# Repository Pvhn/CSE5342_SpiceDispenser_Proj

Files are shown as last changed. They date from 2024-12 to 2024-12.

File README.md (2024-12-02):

# This repo contains the contents of the Spice Mixer Project developed for CSE 5342/4342.

The construction of the repository is as follows:

- Documentation:
	- Contains documents that support the implementation of the source code and hardware
- Source Code
	- Contains all source code for the Spice Mixer
- Hardware:
	- Contains all 3D CAD Files as well as CAM files for the PCB

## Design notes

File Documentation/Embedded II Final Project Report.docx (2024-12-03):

Final Project Report - Automated Spice Mixer

Embedded Systems II

Fall 2024

Group 5 - Ethan Sprinkle, Peter Nguyen, Evan Guinn

# 1. Abstract

The purpose of this project was to design, code, and build an embedded project using a TM4C (TIVA C) microcontroller and external peripherals. For our project, we produced an automated spice mixer capable of dispensing spice recipes containing up to 8 different spices. This is useful for cooking applications allowing a user to quickly dispense and measure multiple spices for a given recipe. Future capabilities of the project were kept in mind during the design process so the project could be added to and improved upon in future iterations.

The concepts and techniques obtained from this project can also be expanded to apply to a wider range of dispenser applications such as pill dispensers.

# 2. System Design & Architecture

The spice mixer consists of the following major components: eight 3D printed spice containers with individual augers, a stepper-motor driven turnstile base, and a servo-actuated motor controlled dispensing mechanism. The mixer utilizes two stepper motors, a servo actuator, and two hall effect sensors to properly rotate and dispense the various spices based on a command from a user. The basic features of the system include the ability for a user to select and dispense a single spice, add/delete recipes, and save recipes. A user can perform any of these commands using a UART interface (such as Putty) to both send and receive information from the microcontroller. Spice recipes are saved using the EEPROM, allowing recipes and spice information to be retrieved upon power loss to the unit.

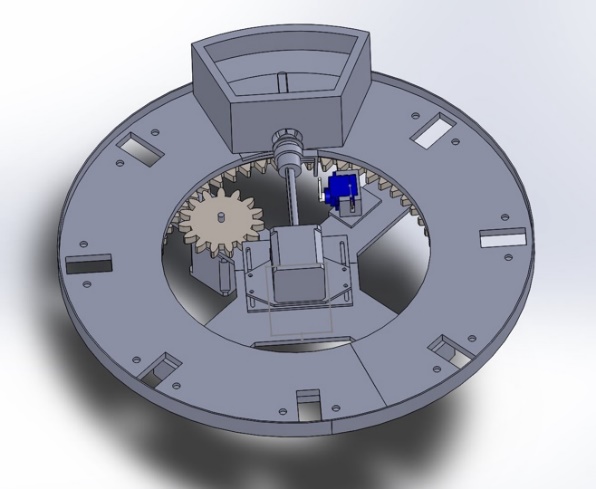
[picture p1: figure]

Figure 1. Spice Mixer CAD Design

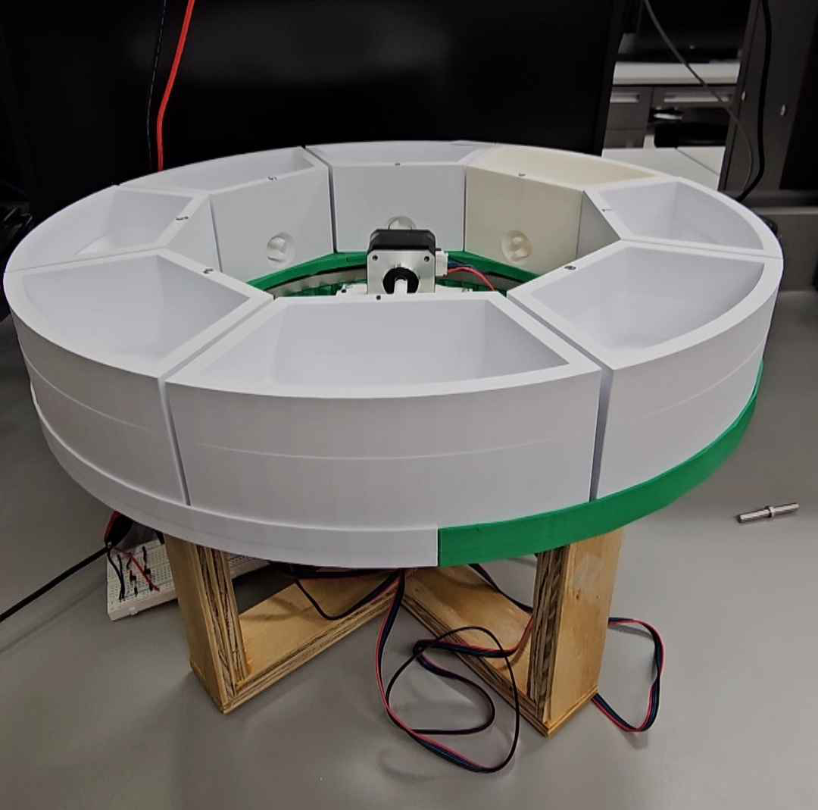
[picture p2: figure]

Figure 2. Spice Mixer

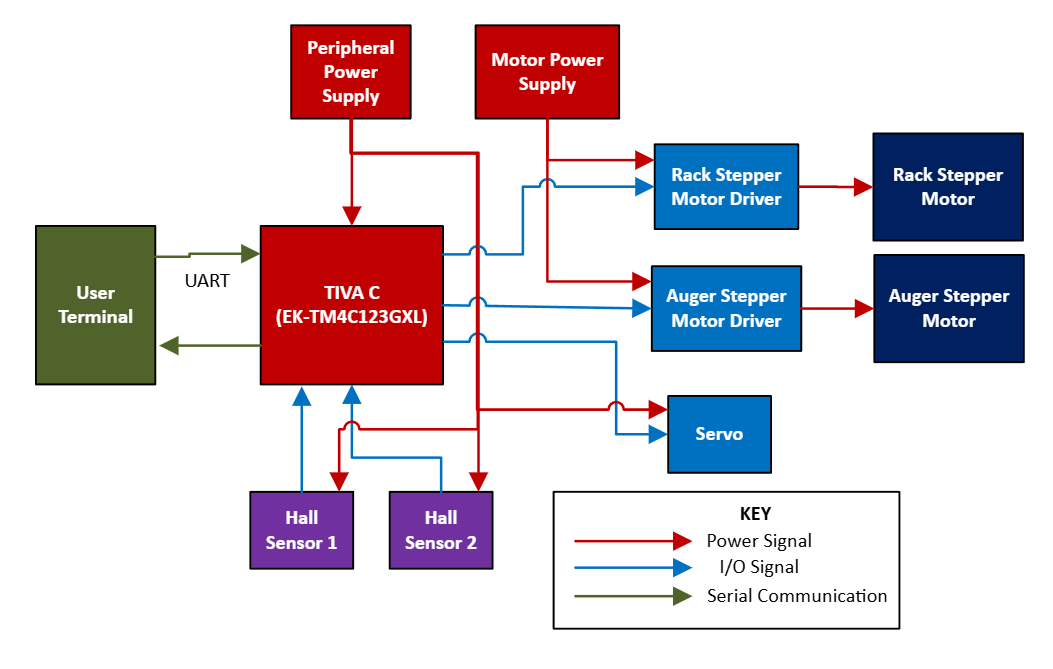
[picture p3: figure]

Figure 3. System Block Diagram

# 3. Implementation

## Hardware

### 3.1.1 Physical Components

#### Auger and Auger Shaft

Physical components of the spice mixer were modeled using SolidWorks. Shown below are the designs of the Auger and Auger Shaft mechanism which is used for dispensing spices. The auger is designed to attach to the inside of the spice holder via a small magnet placed on the end of it. The triangular points are designed to allow connection with the auger motor shaft. The opening is designed to hold approximately a volume of half teaspoon.

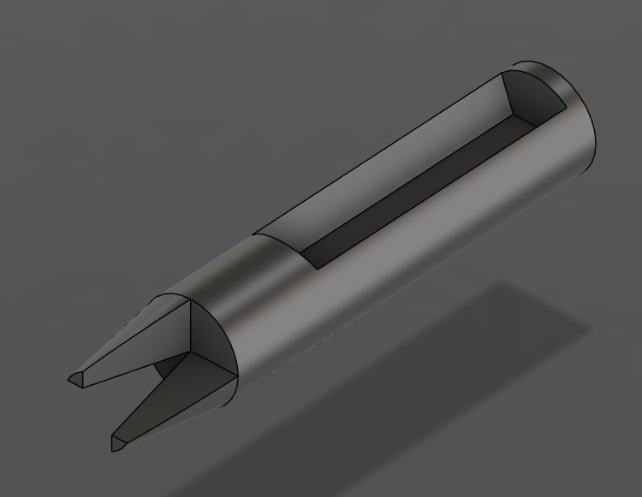
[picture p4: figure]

Figure 4. 3D Model of Auger

The auger shaft that is connected to the auger motor is designed to slide along the motor shaft using the servo. The servo controls a pinion gear which will slide the rack that the shaft is attached to.

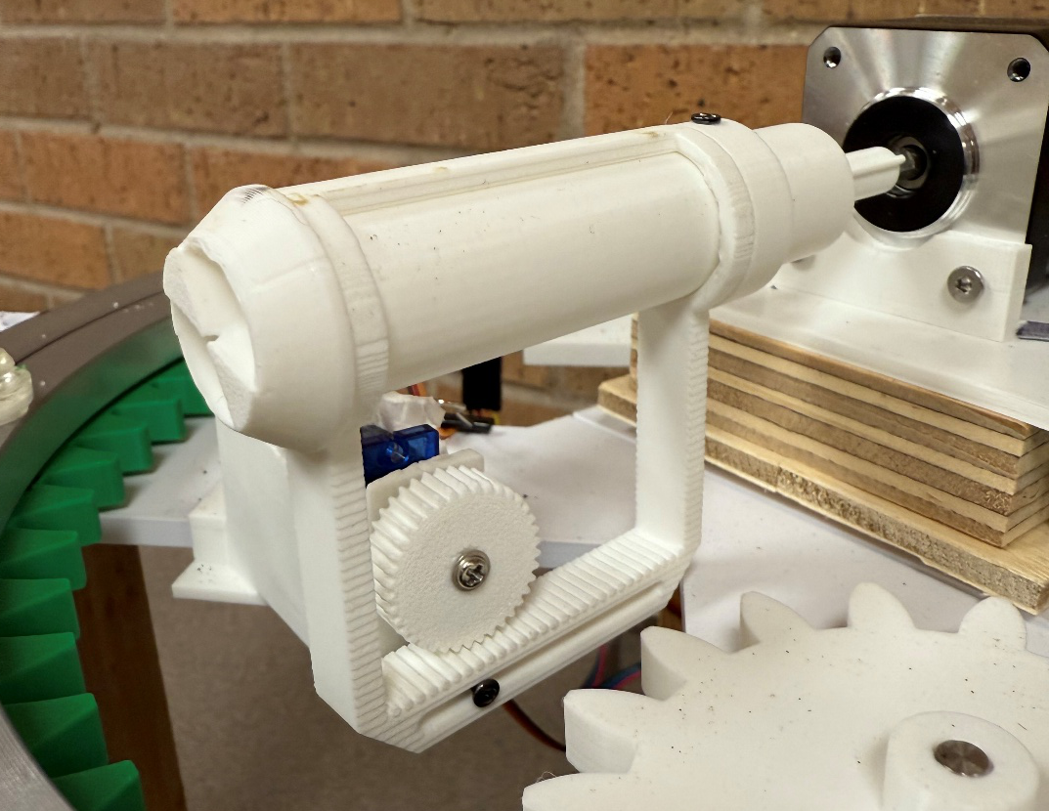
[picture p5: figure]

Figure 5. Auger Shaft and Servo Connection

#### Rack

The entire spice table sits on a turntable which is turned via gears attached to the turntable and the rack motor.

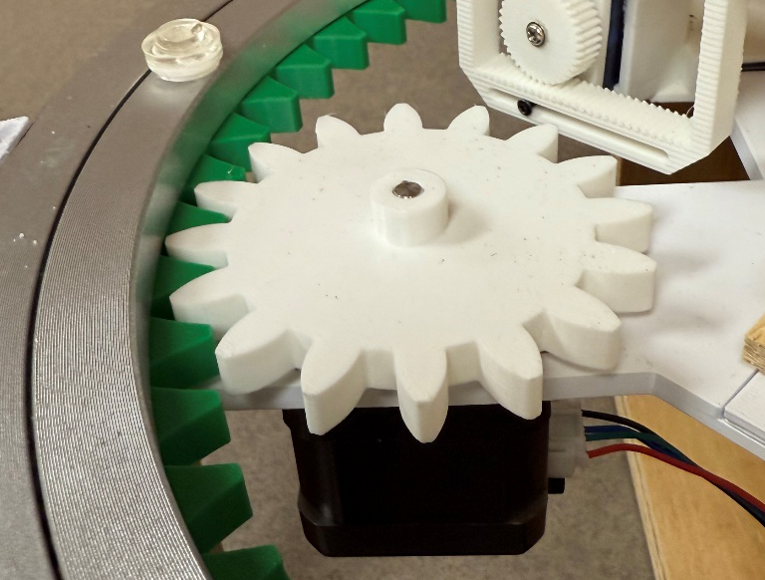
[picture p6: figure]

Figure 6. Rack Motor Gear Mechanism

### 3.1.2 Electrical Components and Peripherals

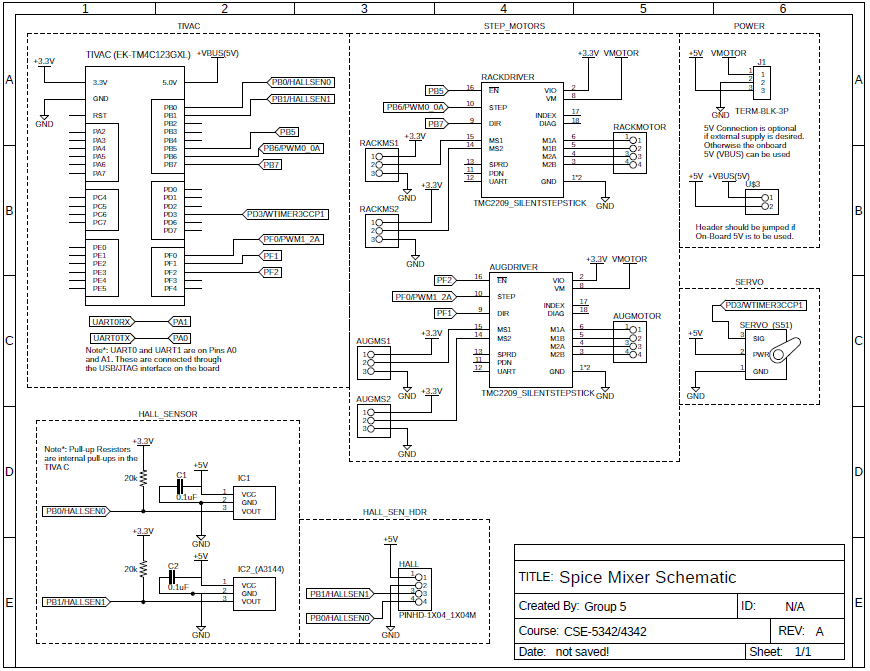
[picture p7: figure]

Figure 7. System Electrical Schematic

The figure shown above shows the overall electrical schematic of the system. The motors chosen for controlling the spice mixer are the 42BYGH NEMA 17 stepper motors. These operate at a nominal voltage of 12V and can be driven up to 1.2A max allowing for the spice mixer to be supplied with power using widely available 12 DC power supplies (commonly used by laptops and other household devices). The motors have a resolution of 1.8 degrees per step or 200 steps per revolution. The stepper motor drivers chosen for the spice mixer are the TMC2209 Silent Step-stick drivers. These are known for their silent operation and include a variety of features including a UART interface for configuring the driver. The drivers also come with on-board current sensing which is important for controlling a stepper motor and avoiding damage to the motors. Additionally, the drivers also allow for the micro-stepping of stepper motors allowing for an increased resolution per step from the base resolution. The TMC2209 allows up to a 256 microstep resolution. For the spice mixer, the configured resolution is 16 microsteps. The extended features of the driver via the UART interface were not used for the current implementation. Each driver requires a minimum of 3 pins for control, these being the step (PWM) pin, the enable pin, and the direction pin. As such at least 2 PWM pins and 4 output pins on the TIVA C are required for driving. Any of the capable PWM pins on the TIVA C can be used for driving. The pins chosen for the spice mixer were originally chosen given that each of the pins had PWM capability. During initial integration it was found that the original chosen drivers (which required 4 PWM pins each) were not suitable for the project application and thus these were replaced with the TMC2209. In consideration of time constraints and to avoid a full re-design, the original pins were re-programmed to work with the TMC2209.

The hall sensors are the A3144 Hall-Effect Sensors. Unlike linear hall sensors which have an analog output, these sensors have a digital output which operate based on an open-drain configuration, where the output pin is pulled to ground upon detection of a magnetic field and open when no magnetic field is detected. The output pins of the hall sensor are connected to input pins on the TIVA C. These input pins are configured to use the internal 20kΩ pull-up resistor to pull the sensor output high while there is no magnetic field detected. The servo used is a generic S51 servo which can be operated off a 5V supply and allows for up to 180 degrees of movement. The servo requires a 50Hz PWM signal with a duty cycle varying from 5 to 10% (pulse of 1ms to 2ms) for varying the angle. Due to the slow PWM rate required for the servo, the PWM pins of the TIVA C are not capable of driving at 50Hz without requiring a clock divisor. However, as this would impact the configuration of the stepper motor drivers, it was decided to use the wide-timers (32-bit) and its PWM output capability for controlling the servo. Communication between the TIVA C and the user is performed via UART. Module UART0 was chosen as this is directly connected to the micro-USB/JTAG output of the TIVA C board. The UART is configured to operate at the standard baud-rate of 115200 bits/s. The user may communicate using any serial terminal such as Putty or Real-Term.

### 3.1.3 Driver Board

A PCB (shown in figure 5) was made to minimize the wiring required for the spice mixer. The PCB has header pins on the bottom of the board allowing it to interface with the TIVA C as a “hat.” The driver board includes a screw terminal for the 12V motor supply and optional 5V terminal for the hall sensors and servo. If an external 5V supply is used, the jumper pin connecting the 5V rail to the TIVA C VBUS rail must be removed. In addition to this the driver board also contains jumper pins for the TMC2209 driver configuration. The pins can be moved to either apply 3.3V or GND to the MS1 and MS2 pins of the TMC2209. These pins determine the microstep resolution the driver will operate at. As stated in the previous section, the 16 microstep resolution (MS1=MS2=3.3V) is used. Refer to the datasheet of the TMC2209 driver for further configuration. The step motor drivers interface to the driver-board via header pins allowing them to easily be removed in the event it needs to be replaced. The PCB shown in figure 4 was produced in-house at UTA by the EE Makerspace Lab. As it was a prototype board, the board does not contain a silk screen or any labeling to indicate the pin connections and polarity. Connections to this board should be verified against the schematic (figure 4).

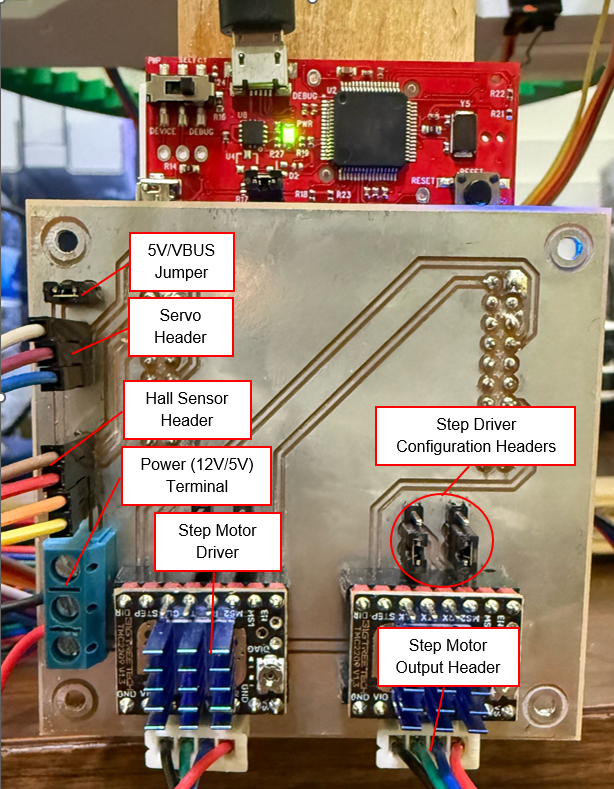
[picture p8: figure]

Figure 8. Driver Board PCB

## Software

The software is broken up into 3 primary modules consisting of the User-Interface module, the Motor Control module, and the EEPROM module. Each of the primary modules are designed specifically for the control and program flow of the Spice Mixer. The primary modules may each contain smaller secondary modules which are designed for the purpose of performing a specific action such as moving a stepper motor, reading/writing to the EEPROM, and parsing for user commands. These secondary modules can be readapted for other purposes.

### 3.1.4 UART

User commands are sent over the UART protocol from an input device, such as a computer (in the case of the prototype) or touchscreen. For the prototype, the baud rate used is 115,200, with 8N1 and a 16-entry FIFO. These commands are sent as plain text, which is then parsed into a sequence of ‘fields’ delineated by spaces and stored in a USER_DATA structure. During parsing, the positions and number of fields are stored alongside the original plain text for use by the command functions in UIControl.

### 3.1.5 User-Interface and Main Program

The user-interface/UART is designed to continuously poll for user commands in the main loop of the program. When a command is received from the UART, the user-input is parsed (as described in the UART section) and the first argument is compared and validated against a list of known commands. Any command that is not recognized by the UART interface will result in a notification error to the end user and the display of the “help page” which will list all known commands and their usage/syntax. In addition to being a known command, some commands require additional initial arguments (fields). These required minimum fields will also be validated at the time of processing the user command. An error message will also be displayed for the following conditions:

- Incorrect parameters used when entering a UART command
- The amount of spice remaining in a container is less than the amount required by a recipe
- A Recipe Name does not exist in EEPROM
- A Spice Name does not exist in EEPROM

Figure 9 shows the basic flow of the main loop. The valid system commands are discussed in the sections below.

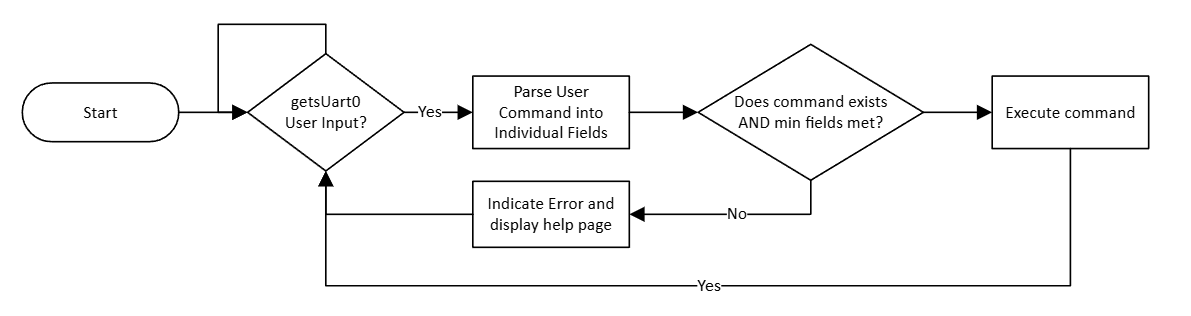
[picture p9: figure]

Figure 9. Main Loop Flow Diagram

#### Spice Command

The spice command is the basic command to dispense a single selected spice. The syntax of the spice command is as follows:

- spice <spice name> <quantity>

The user must provide the name of an existing spice followed by the quantity. If the name provided does not match any of the known spices, an error will be indicated, and the command will abort. The quantity will be checked to verify there is enough spice remaining for the requested quantity. This is done by reading the remaining quantity from the EEPROM and then comparing it. If there is an insufficient amount, an error message will be indicated to the user and the system will then request additional user action to determine if the user would like to proceed with the dispense or cancel the action. The user may respond by pressing any key to continue with the dispense or typing in “cancel” to abort the command. On completion of the dispense sequence (discussed in the Motor Control section), the remaining quantity will be updated in the EEPROM.

Note that, on start-up, this command will not be accessible to the user until the home command is performed. (See Home command below). This is to ensure the system has accurately determined the home status before attempting to dispense. Any attempts to use this command before homing is performed will result in a warning message to be indicated to the user. The command will not be performed.

#### Recipe Command

The recipe command is an advanced command to dispense multiple spices. The syntax of the recipe command is as follows:

- recipe <recipe name>

The user must provide the name of an existing recipe. No other arguments are required. If the name provided does not match any of the known spices, an error will be indicated, and the command will abort. If the name exists, the contents of the recipe will be extracted from the EEPROM. Prior to dispensing, each spice element of the recipe will be verified to ensure there is enough remaining. Like the spice command, if there is not enough, an error message will be indicated to the user and the system will prompt the user to either continue or cancel the command. This is repeated for every element in the recipe. The end of a recipe is determined either when the requested quantity is 0 (indicating an empty slot) or the max slots (8) have been dispensed. On completion of the dispense sequence, the remaining quantity of each spice is updated in the EEPROM.

Note, on start-up, this command will not be accessible to the user until the home command is performed. (See Home command below). This is to ensure the system has accurately determined the home status before attempting to dispense. Any attempts to use this command before homing is performed will result in a warning message to be indicated to the user. The command will not be performed.

#### View Command

The view command allows for the user to view a list of existing spices and their quantities or a list of stored recipes. The user can access either by indicating “spices” or “recipes” as the second argument. The syntax of the view command is as follows:

- view <items>

#### Check Command

The check command allows for the user to check the contents of an existing recipe. The user must provide the name of an existing recipe. The command will extract the contents of the recipe from the EEPROM and display each element and their quantities (in teaspoons). The syntax of the check command is as follows:

- check <name>

#### Save Command

The save command allows for the user to save a new recipe or update an existing recipe. If the name of the recipe already exists, the system will notify the user that the recipe already exists and whether they would like to continue or not. If the user chooses to cancel (by typing in cancel) then the command will abort. If the user chooses to continue, the command will begin prompting the user for entries in the recipe. If the name does not exist, the command will validate that the name entered is less than 16 characters. If it is not, the command will be aborted. If the name is within the required length, the system will begin prompting the user for entries in the recipe. The syntax of the initial command is as follows:

- save <recipe name>

For each entry, the user must provide the name of an existing spice along with a quantity less than 1 cup (48 teaspoons). The system will validate that the user enters a valid name and quantity. If either is invalid, an error message will be indicated to the user. Unlike other errors, at this stage, the error message will not abort the command. Instead, it will loop and prompt the user to try again and enter a valid entry. This will continue until either a valid entry is provided or the user cancels. The syntax of entries is as follows:

- <spice name> <quantity>

At any time, the user may type “done” instead of an entry to indicate that this is the end of the recipe. Alternatively, the user can type “cancel” to abort the command. If the user enters a spice name that they had previously already entered, the user will be notified and prompted if they would like to overwrite their previous entry. If the user chooses to continue, then their newest entry will be stored. The system will continue to prompt the user until either “done” is entered or the max number of elements (8 spices) is entered. On completion, the recipe is stored into the EEPROM. If the recipe is an update of an existing recipe, the number of stored recipes (in the EEPROM) will not be incremented. Otherwise, it is incremented. Additionally, the name of the new recipe is copied to the local list/dictionary of stored recipes.

#### Delete Recipe Command

The delete recipe command allows for a user to delete a stored recipe from the EEPROM. The syntax of the delete recipe command is as follows:

- delete <recipe name>

The user must provide the name of an existing recipe. If the name does not exist, an error will be indicated to the user and the command will be aborted. If the name does exist, the system will then ask the user to confirm that they want to delete the recipe. The user must type the keyword “delete” to continue with the removal. If any other word is entered, the system will abort the command. On entering the keyword, the system will remove the recipe from the EEPROM. Due to the direct indexing and accessing of the recipes, along with deleting the recipe, the system must subsequently copy each existing recipe below the deleted recipe and move them up one index if the recipe is in the middle of the block of existing recipes. This method is not ideal as it requires multiple read and writes of the EEPROM thus decreasing the overall usage life of the EEPROM. However, this was the most “efficient method” and as such was used. Future work may improve upon this method.

#### Refill Command

The refill command allows for the user to refill an existing spice with a specified quantity. The syntax of the refill command is as follows:

- refill <spice name> <quantity>

The user must provide the name of an existing spice followed by the quantity. If the name provided does not match any of the known spices, an error will be indicated, and the command will abort. The quantity will be checked to verify if it is less than the max allowed quantity. If the quantity is greater than the max allowed quantity, then a message will be indicated to the user indicating that the quantity they have entered is greater than the max and the system is assuming that they meant to fill the spice to the max quantity. After validation, the command will then subsequently update the remaining quantity of the spice in the EEPROM with the requested quantity.

#### Change Spice Command

The change spice command allows for the user to change or update the name of an existing spice. This is mainly used if the user has filled a spice slot with a different spice from the one currently stored in the system. The syntax of the command is as follows:

- change

On entering the command, the user is prompted for the slot value they would like to update. This slot must be between 0 and 7 (max of 8 slots). If an invalid slot number is provided, an error message will be indicated to the user and the system will prompt the user to try again and enter a valid slot number. This will repeat until either a valid slot number is entered, or the user chooses to cancel. On a valid slot number, the system will repeat the name of the spice that is currently stored in the slot number the user had entered and ask the user to confirm that they would like to continue with changing the name. If the user chooses to continue, the command will then prompt the user to enter the name of the new spice. This name must be less than 16 characters and must be one continuous word. If the entered name is invalid, an error message will be indicated to the user and the system will prompt the user again to enter a valid name. On a valid name entry, the system will write the new name to the corresponding slot in the EEPROM as well as update the local list/dictionary of known spices. The system will then ask if they would also like to update the quantity of the slot they had chosen. The user must type “done” if they wish not to continue. Otherwise, the system will begin prompting the user to enter the quantity of the spice. The user may enter cancel if they change their mind, and the command will then abort. Otherwise, if a valid quantity is entered the remaining quantity of the spice in the EEPROM will be updated with the new requested quantity.

#### Home Command

The home command performs the homing of the rack. The syntax of the home command is as follows:

- home

The command will simply perform a call to the home function in the motor control module to perform the homing. Details of the homing method are discussed in the Motor Control section below. On failure of homing the system will indicate an error message to the user to verify there are no obstructions and to either try again or power reset the system.

#### Reset Command

This command allows for the user to perform a system reset. The syntax of the reset command is as follows:

- reset

The reset command is to be used in the event of an EEPROM failure or some other system type failure. This command will reset all spices to the default first start-up values and will also remove all stored recipes. On entry to the command the user will be asked to confirm that they want to proceed with the system reset. The user must type in the reset keyword “RESET_SYSTEM_X342” to proceed with the reset. Any other value entered will result in the command to be aborted. On the entering of the keyword, the system will re-initialize the EEPROM with the default spice data (like the initialization that is performed when the system is powered on for the first time). As this reset is destructive, once the reset is complete, the system will prompt the user to restart the system. The program will then enter an infinite loop, thus forcing the user to power-cycle/restart the system.

#### Stop Command

The stop command allows for the user to remove power from all the primary stepper motors. The syntax of the stop command is as follows:

- stop

On entry of the command, power to both the Rack and Auger motors will be removed. Note, homing must be performed following the usage of this command before spice or recipe commands can be used as once the motors are turned off, the position of the rack will effectively be unknown.

### 3.1.6 Motor Control

This section discusses the Motor Control module of the spice mixer. The motor control module includes all functions necessary for controlling the stepper motors and the servo, as well as reading the inputs from the hall-effect sensors.

#### Dispense Sequence

When a recipe or spice is selected to be dispensed, there are 4 major aspects of the dispense sequence. These are: positioning the rack, engaging the servo, commanding the auger dispense, and the disengaging of the servo.

The microcontroller first checks its current position and compares it to the desired position of the selected spice. The program will perform a delta calculation to obtain the shortest distance and determine if it should turn clockwise or counterclockwise (whichever is closer to the desired position). Once the delta has been calculated, the required angle is converted into microsteps to be used by the PWM Interrupt handler for commanding the rack motor. Note, the chosen microstep resolution for the Spice Mixer was 16. The conversion from an angle to microsteps would normally be performed using the following equation:

(∆angle)/(200*16) (1)(Angle to Microsteps Equation)

Where 200 as recalled is the number of full-sized steps for a full rotation of the motor shaft. However, since the rack motor is connected to the rack via a gear, the conversion must also account for the gear ratio. As designed, the gear ratio is 56:15 where the rack motor must make 3.5 turns for a full rotation of the rack motor. The previous equation now becomes:

(∆angle)/(200*16)*GearRatio (2)(Angle to Microstep w/ GearRatio Equation)

Once all rotation steps have been completed (and the auger is aligned with the shaft of the motor dispenser), the servo actuates the auger motor shaft into place with the auger of the spice dispenser. The auger will then be commanded to turn the desired number of rotations. Note, a full rotation of the auger motor equates to a ½ teaspoon of the selected spice. The rotation command is like the rack motor except that the auger motor only needs to rotate one direction, so the delta calculation is simply calculating the total number of microsteps per requested rotations. Equation 1 can be used for this conversion. Once rotation is complete, the servo will then disengage the motor shaft from the auger and the process will repeat for any additional spices in a recipe. The figure below shows the overview of the dispense sequence. Note, due to the auger shaft sometimes not being properly aligned with the auger, an auger offset was added in the software. The auger motor will complete the requested number of rotations and then will rotate an additional 20 degrees to offset the auger. The servo will disengage at this point. After disengagement, the auger motor will rotate the shaft back 20 degrees. This placement positions the auger approximately in the middle of the opening of the auger shaft thus increasing the likelihood of a successful connection.

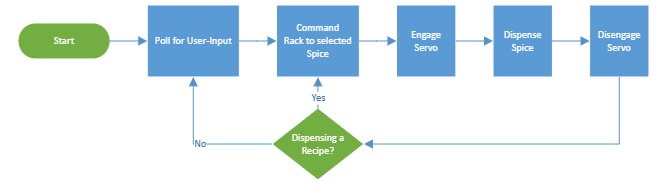
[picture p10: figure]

Figure 10. Dispensing Sequence Flowchart

#### Stepper Motor Control

The stepper motors are controlled by the TMC2209 stepper motor drivers. These require at least 3 inputs which are: STEP, EN, and DIR. The step pin is the PWM input which is used to control the speed and step sequencing of the stepper motors. Speed itself is not controlled by varying the duty cycle. Instead, speed is controlled by increasing or decreasing the PWM frequency since for each pulse detected the driver will increment the step index to move the motor. The duty cycle output from the TIVA C is fixed at a 50% duty cycle. The EN pin is the enable pin and is used to enable/disable the stepper driver output. The DIR pin is the direction pin and is used to control the direction of the motor (CW = 0, CCW = 1).

The commanding and controlling of the PWM outputs are performed via a PWM Interrupt. The beginning of a motor command starts with the calculation of microsteps required by the command. For the instance of the rack motor, it will be provided a slot position (0-7) that it needs to move to. The slot position is then converted to the angle on the rack with respect to the home position. The difference between the requested angle and the current position is taken. The delta is used to determine the direction of rotation (CW or CCW, whichever is the shortest distance). For the instance of the auger motor, it will be provided the number of rotations. The angle/number of rotations is then converted to microsteps of which are provided to the PWM Interrupt Handler for sequencing. Once calculation is complete, the EN pin is cleared to enable the stepper driver output and the PWM Interrupt is enabled to begin the driving of the motor. The main program at this point enters a while loop and will poll the status of the motor while it waits for the step command to be completed by the interrupt handler.

Figure 11 Stepper Motor Control Flowchart

The PWM Interrupts are configured to interrupt when the generator value reaches 0. This is used since the duty cycle is always fixed at 50%. On an interrupt, the handler will determine if it needs to run based on the step count (previously calculated by the main program). If the step count is greater than 0, this indicates the interrupt should continue to run and sequence the step pulse to the driver. With each interrupt, the step count is decremented until it reaches 0, at which point the interrupt handler will disable further interrupts and disable the PWM output to the stepper driver. In addition to decrementing the step count, the interrupt handler is also responsible for updating the speed of the motor (by setting the LOAD and CMPX registers of the PWM module to vary the frequency). This ensures a consistent PWM output as the interrupt handler will sync the output. The interrupt handlers are mostly the same for both the stepper motors with the exception being that the rack motor has acceleration control. The choice of using interrupts vs actively managing the motor control in the main program was made with the intention of performing other tasks such as active homing or failure handling cases, such as when the user may issue a “stop’ command.

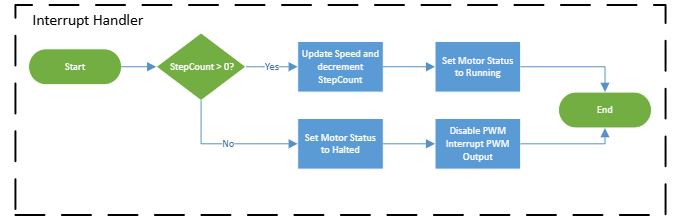
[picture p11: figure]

Figure 12. PWM Interrupt Handler Flowchart

To allow for a common architecture and provide the potential for expansion, all necessary data for motor control is stored in a structure type. A motor can be “registered” into the system by adding it to the Motor Data array. Each motor has the following available properties:

- Run Status – (OFF, HALTED, RUNNING, FAILED)
- Direction – (CW, CCW)
- Home Status – (NOTHOME, NEARHOME, HOME)
- Steps - (The number of steps the motor needs to move)
- Position – (Not used in current implementation. Was kept with the intention of using for active position feedback).
- Speed – (speed in rpm)

Not all properties are used by a motor (such as the Home Status and position for the auger motor). This motor data is only accessible by the stepper motor control module. This was done to limit access to important motor control data. “Get” functions were developed to allow external modules to read the status.

Acceleration control of the rack motor was added to improve accuracy and prevent skipping of steps during start and stop maneuvers due to the inertia of the rack. A simplified flowchart of the acceleration control algorithm is shown below.

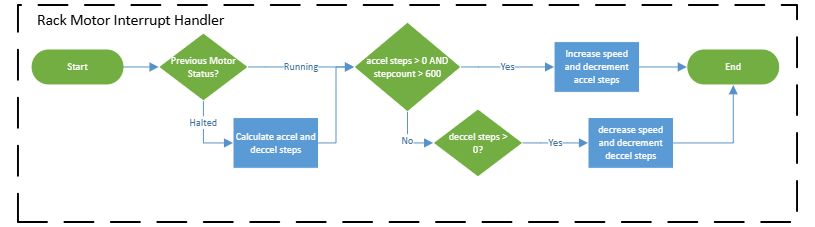
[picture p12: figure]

Figure 13. Acceleration Control Flowchart

The algorithm begins by determining the previous status of the motor. If the motor status was previously halted, then the acceleration/deceleration steps are calculated. This is simply the amount of command steps divided by 2 for both (i.e. the motor will accelerate for half of the steps and then decelerate for the remaining half). The speed will also be set to the minimum RPM (6 RPM). In the subsequent iterations, the speed of the motor will slowly be increased by a constant factor of 0.03125 RPM (corresponding to 1 RPM increase for every 1.8 degrees). The speed will continue to increase until either the motor has reached the full commanded speed, the total number of acceleration steps has been performed, or the remaining commanded steps is less than 600. The 600 remaining commanded steps condition was added to improve control for smaller moves (such as that performed during the homing offset) as the motor has less time to decelerate in these moves. Once acceleration is completed, the motor will then begin to decelerate as it approaches the midpoint between the final position. Like the acceleration component, deceleration will decrease the speed by a constant factor. This factor is determined based on the final speed of the motor during acceleration divided by the total deceleration steps. This is done to prevent the motor from reaching the minimum speed too early in the deceleration, resulting in the motor moving into position extremely slowly during longer commands.

#### Rack Homing

On startup and/or after a stop command was issued, the Spice Mixer will require the user to initialize the calibrated “home” position before any dispense action can be performed. The homing method utilizes the mid-point between two hall effect sensors to determine the “home” position for additional accuracy. Using a single sensor may incur directional error since the hall sensor may indicate detection even if the magnet is not directly over the sensor, so by using two sensors the directional error is cancelled out since the mid-point between the two sensors will always be the mid-point regardless of the direction the rack was moving. A magnet placed under the turn table is used to trigger the sensors.

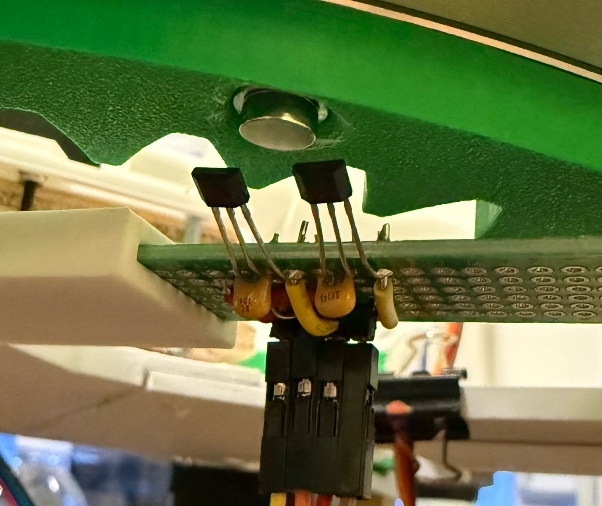
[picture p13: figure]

Figure 14. Hall Sensors and the Homing Magnet

Due to the placement of the sensors, the mid-point of the sensors is not the true home-point. Once the hall sensors have both detected the magnet, the rack motor must be commanded some additional steps to put it in the true home position.

The home state has 3 possible states: NOT_HOME, NEAR_HOME, and HOME. When one of the sensors detects the magnet, the home state will transition to NEAR_HOME indicating to the system to prepare to stop. When both sensors detect the magnet, the home state will then transition to the HOME state indicating to the system to halt the rack motor. If the home state has transitioned to NEAR_HOME and one or more sensors stop detecting the magnet, the home state will transition back to NOT_HOME, indicating to the system to speed up and continue rotation.

The checking of the hall sensors is performed via a GPIO interrupt. Since the time at which the home point is detected is critical to obtaining an accurate home position, the usage of interrupts for this is required. The interrupt is configured to trigger on both rising and falling edges. Recall from the Hardware implementation section that the Hall sensors are active low and thus their logic states are inverted. The detection of the falling edge allows us to determine when a sensor has detected the homing magnet. The rising edge allows us to determine the opposite. This is mainly used for the scenario that the hall sensor stopped detecting the magnet and reset the home status to indicate from NEAR_HOME to back to NOT_HOME. Note, this interrupt will continue to run even if a homing command is not currently being performed. This has minimal impact on the system resources as the magnet is placed in a specific position and thus it will not constantly interrupt (unless there is a failure). The usage of the interrupt may be useful in future work to perform active homing which may be used to provide positioning feedback to adjust for any error that may have incurred during normal operation.

On the issuance of a home command, the program will command the rack motor to perform 3 full rotations at a speed of 10 RPM. It will then wait approximately 1ms for the motor to begin moving to ensure an accurate motor status is obtained. The function will then continue to periodically poll the home status (that is set by interrupt) and the run status of the rack motor to determine if homing was successful or failed. If the run status of the motor indicates HALTED and the home status indicates NOT_HOME, then this indicates that the rack performed 3 full rotations before home was found. In the event of a home failure, an error code of 0xDEAF is returned to the main program for processing and failure management. If the home status indicates HOME, the function will then command the rack to rotate an additional number of steps to align with the true home position. Note, the number of steps is largely dependent on the placement of the hall sensors. For the current implementation this offset was found to be approximately 32 degrees counterclockwise.

#### Servo Control

The servo used to actuate the auger motor shaft is controlled using the Wide-Timer 3 PWM Output of the TIVA C. Unlike the Stepper motors which used an interrupt routine for controlling and maintaining the step count, the servo only requires us to set the necessary duty cycle with no further action needed. The servo operates at a rate of 50Hz and requires a pulse lasting between 1ms to 2ms (0 to 180 degrees). The conversion from desired angle to load value to be written to the TxMATCHR register of the wide timer is calculated as follows:

load value=[(desired angle)/180*((SYSCLOCK)/(50Hz)*0.1)]+((SYSCLOCK)/50)*0.025

SYSCLOCK is simply the frequency of the system (40Mhz for our case). The 0.025 factor is derived from the 2.5% duty cycle bias for a 0-degree command.

### 3.1.7 EEPROM

This section discusses the EEPROM Control module of the spice mixer. The EEPROM module is used to store system data for the spice mixer and most importantly recipes. The EEPROM is a non-volatile type of memory, i.e., it retains its data even when power is removed.

The EEPROM of the TIVA C is distributed into “blocks” where each block contains a specified number of 32-bit words. The TIVA C contains 16 total blocks with each containing eight 32-bit words. This equates to a total of 128 32-bit words. Read and write access of the EEPROM is performed in 32-bit words. The data used by the spice mixer, however, does not need to be 32-bits. To maximize memory storage, the spice mixer data is stored using smaller 16-bit words and bitfields. The memory layout of the EEPROM is shown below.

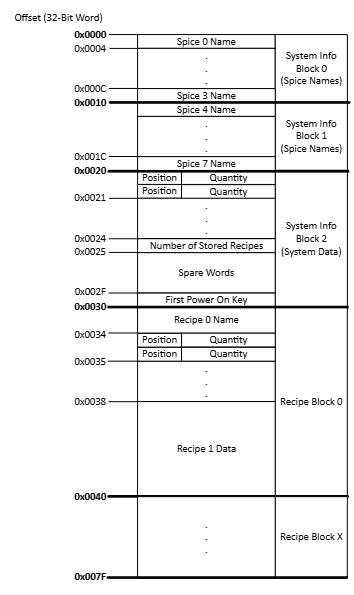
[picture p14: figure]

Figure 15. EEPROM Memory Layout

#### System Information Blocks

The system information blocks (blocks 0-2) contain data needed for operation of the spice mixer. This includes spice names, spice quantities, and the total number of stored recipes. Each of the 8 spice names are allotted four 32-bit words of memory, allowing for up to 15 characters plus the null character to be stored. The spice data is stored in a single 16-bit word. The spice data word is further split into the position and quantity bits with position being the first 4 bits of the word and the remaining 12 bits being the quantity. As the max slot capacity of the current implementation is 8, it was decided to only use 4 bits. However, this can be increased to 8-bits to support an increase in slot capacity. The quantity bits allow up to a quantity of 4096 to be stored. This is more than sufficient for the needs of the system as the max capacity is only 96 (half teaspoons). The number of stored recipes is also stored as a single 16-bit word. The full 16-bit word is not needed to store the number. However, it was decided to use the full word to simplify the reading of the number. In addition to this data, there is also a First Power-On Key that is stored in the system information block. This key is used to initialize the EEPROM with default spice data/names for the case of when it is the first time powering on the system as the EEPROM will not have anything stored in it yet. After this initial power-on, a keyword of 0xBEEF is written to the EEPROM to indicate for the next start-up that it is already initialized and should use the data currently stored in the EEPROM. The remainder of block 2 is unused. This is not only to maintain separation of system information and the stored recipes but also allows for future expansion if additional slots are added to the mixer.

#### Recipe Information Blocks

Recipe Information is stored in blocks 3 to the end of the EEPROM. As seen from the memory map, each recipe data contains the name (15 characters plus null) of the recipe, and 8 16-bit spice data words (one for each capable slot). This results in each recipe requiring a total of eight 32-bit words. Given this and the max EEPROM size of 128 32-bit words, the system has the capability to store up to 26 recipes. Not all 8 spice data words need to be used in a recipe. Unused words will be written to 0 allowing for the simple detection of the end of a recipe (when the quantity is 0). Additionally, spice data does not necessarily need to be stored in order of slots as the position bits will contain the necessary value to determine which spice to dispense.

#### Reading and Writing to EEPROM

Since the EEPROM is only accessible in 32-bit words, special considerations must be made when reading and writing to the EEPROM.

Reading from the EEPROM is simpler than a write request in that we do not need to worry about data loss. For instance, say we want to read the spice data for slot position 0. From the memory map this is stored at offset 0x0020. To initiate a read, we must write to the EEBLOCK and EEOFFSET registers. The EEBLOCK is provided the desired block number our data is in (block 2 in this instance). The EEOFFSET register is the 32-bit word offset we would like to read from (Word 0 in this instance). The read data will be returned as a 32-bit word. Per the memory map, we know that spice data for position 0 is stored in the lower half of the 32-bit word so we only need to read the data from that half. The upper half of the 32-bit word (which contains spice data for position 1) is simply ignored.

Writing data to the EEPROM requires the additional step of reading the data currently in the EEPROM. Since writing to the EEPROM is performed in 32-bits, we must ensure that the lower or upper half of the word we are not writing to is not overwritten with zeroes. By first reading the full 32-bit word and then making a local copy, we can then write data to the desired upper or lower half and then write the full 32-bit word back, thus maintaining the data. Additionally, all functions that write to the EEPROM will also return an error code from the EEPROM if the EEPROM failed to write. This error code may be used for notifying the user of a system issue and have them attempt to restart the Spice Mixer to attempt to reset the EEPROM.

# 4. Results & Testing

The physical components of the project were first modeled in Solidworks3D to ensure proper design dimensions and functionality. Parts were then 3D printed using PLA material and then tested for form, fit, and function with the rest of the assembly. Parts that failed were adjusted in the CAD software and reprinted. A wooden frame was used to elevate and hold the Spice Mixer assembly.

Software development was shared across the team using a git repository. Branches were created, tested, and merged by individual group members for the development of three main functionalities: EEPROM, UART Interface, and Motor Control. The Motor Control function was used to test and calibrate the physical components to ensure they would work properly with the software. Prior to validating the motor control with the hardware, the debugger was used to validate proper commands and outputs and ensure no hazardous faults (such as a short to ground) were being done. This was performed by verifying the state of the output registers. Additionally, appropriate timing/frequency were verified using an oscilloscope.

Once the software was validated, the motor control functions were integrated with the hardware. Electrical components and wiring were verified using a breadboard. The prototype PCB was developed afterwards once all connections were verified. The EEPROM storage was validated by first developing and testing the write functions by writing test data to the EEPROM. The read functions were then developed and tested by reading the data from the EEPROM. Proper functionality is confirmed when the value that was written to the EEPROM is repeated back by the read functions. The UART interface commands were tested individually to ensure validation of commands and ensure consistent user operation.

## Integration Findings

Integrated testing revealed some design flaws in the system. Some of these issues were corrected while others are documented here with the intention of improving it in future work.

During initial integration it was found that the stepper motor drivers initially chosen were not sufficient for the application. The drivers lacked current sensing/limiting which is critical for stepper motor control and preventing damage to both the motor and the system. This issue was corrected by choosing proper drivers (the TMC2209). Due to the difference in requirements for driving the motor control code was completely redesigned to work with the TMC2209.

Initially, the rack motor had no acceleration control. Instead, it was immediately commanded to the requested speed (like the auger motor). This was found to cause the rack motor to skip steps during start and stops resulting in inaccurate positioning during both homing and regular operation. This issue was corrected by implementing the acceleration control (described in the Motor Control section).

Variances in the 3D components led to inaccuracies in positioning. For example, it was noted that at certain positions in the rack rotation, the rack would “rub” against the outer wall. This indicated that the rack was not entirely circular. Due to time constraints, this issue was not corrected. It was also noted that the stepper motor provided enough torque to overcome this resistance and as such no further action was taken.

The original design of the auger shaft and auger required that the positioning of the shaft was perfectly aligned. This mostly resulted in the auger shaft failing to engage the auger. This issue was mitigated through both hardware and software. The hardware mitigation was to increase the area of the auger shaft. The size of the auger shaft was slightly increased thus in turn increasing the opening for the auger to connect to. The software mitigation would offset the auger screw, and then rotate the auger shaft back in the opposite direction by the same distance to position the opening of the shaft approximately in the middle of the auger screw, thus increasing the chances of a successful connection.

The flat bottom of the spice holders results in some of the contents not being fully dispensed as there is nothing to push it into the auger opening. As re-designing this would require significant redesign of the current structure, it was decided to defer this issue for future work as the purpose of this project was to develop a prototype.

# 5. Conclusions & Future Work

The main goal of this project was to design and build a functional prototype spice mixer, where additional capabilities could be added in the future to improve upon the original design. To reduce printing material costs and simplify testing, the current iteration of the mixer is limited to 8 different spices. This amount could easily be doubled to 16 containers by simply reducing the size of the current containers and updating the source code, which was designed to be easily configurable. Furthermore, the current augers were designed to dispense in ½ teaspoon amounts, but this value could be lowered by either reprinting the augers with smaller buckets, or by adding blocks to the augers to reduce their overall capacity. Additionally, with the proven functionality, focus can also be placed on improving the design of the spice holder to ensure all spices are dispensed. This may include designing so that the inside sharply slopes inward towards the auger opening thus allowing for the contents of the spice holder to naturally fall into the opening via gravity.

Currently, there is not a precise method to detect the amount of spice remaining in a container beyond a rudimentary decrement method for each auger rotation. By using this method, the system assumes that a full amount is dispensed with each auger rotation and cannot account for scenarios where the full amount is not dispensed, such as with clumping of powdered spices. Conversely, if another peripheral such as a weight scale were added, there could be a check between the expected and actual weights and the mixer could account for the calculated difference.

The UART interface provides a cheap and quick method to communicate with the spice mixer; however, it is not very user friendly. An ideal solution would be to replace the UART interface with an LCD touchscreen equipped with a GUI. This would allow easier parsing of data such as remaining spice levels, current recipes, and recipe modification. A more advanced interface could also include voice activation capability, allowing the user to speak commands to the mixer.

As previously discussed, the drivers used for the project contain advanced capabilities which can be accessed via the UART. These capabilities include stall detection and step indexing for positioning feedback. As these drivers were selected late in the project, the full capabilities of the drivers were not utilized. These features may be beneficial in providing enhanced positioning accuracy for the rack as well as for safety/failure management.

Overall, the project was designed specifically for dispensing spices. However, the concepts as well as the code baseline can easily be re-adapted for any number of dispenser type applications.

# 6. Appendices

## Source Code Repository

The following is the link to the GitHub repository containing the work described in this report. This includes all source code, documentation, and 3D CAD and CAM files.

https://github.com/Pvhn/CSE5342_SpiceDispenser_Proj.git

## Schematics and PCB Files

Development of the electrical schematic and PCB were done in Fusion 360. The following link provides copies of these files. NOTE: Fusion 360 is required for proper viewing and editing. In addition to these links, these files can also be found in the repository

Fusion 360 Project:

https://a360.co/3CVfpxP

Electrical Schematic:

https://a360.co/3AWSpOs

PCB Design:

https://a360.co/3ViIjOJ

## Demo Video

Attached is a video demonstrating the different commands. This video can also be found in the Source Code Repository (See Appendix 6.1).

Commands in the video are shown in the following order:

1. home
2. view spices
3. spice xxx
4. view recipes
5. check CAJUN
6. recipe CAJUN
7. view spices
8. save CHICKEN
  1. Saving a new recipe. For demo purposes the recipe is a random selection of spices with quantities 1,2,3, and 4.
9. view recipe
10. check recipe
11. recipe CHICKEN
12. delete CHICKEN
13. view recipes
14. change
  1. Shown in the video we are swapping out slot 2 (previously GARLIC) for our new spice “PICKLE”
15. refill SAGE 20

Link to demo video: EE5342_SpiceMix_Demo.mp4 (https://mavsuta-my.sharepoint.com/:v:/g/personal/peter_nguyen3_mavs_uta_edu/EVefTSrf9KpFvghp_Y4DllgBElhwOAp0LO3sR-mjClhxzw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)

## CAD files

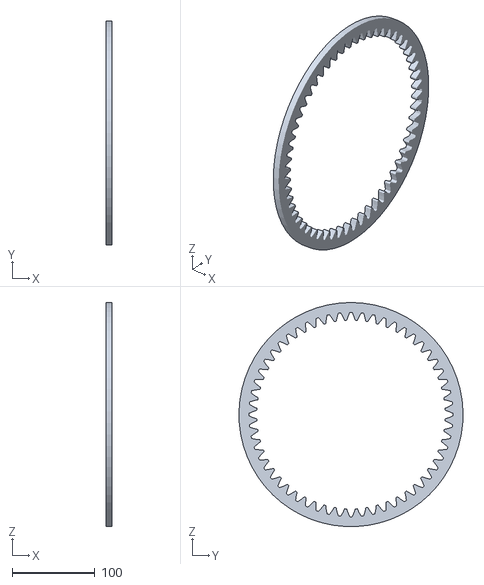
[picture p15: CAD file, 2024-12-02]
Hardware/CAD_Files/Internal gear.STL
7.62 x 271.4 x 271.3

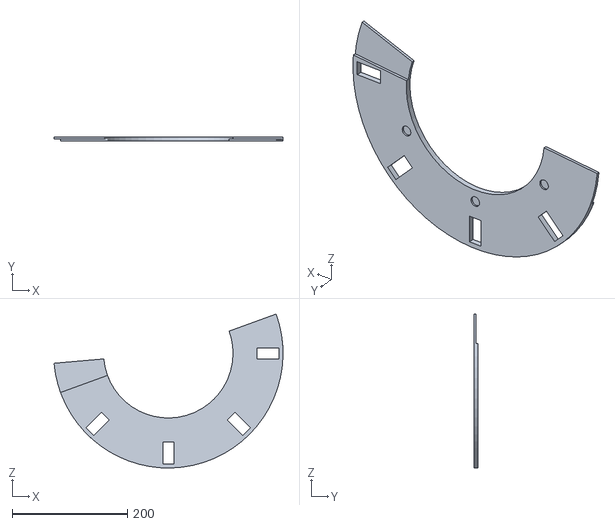
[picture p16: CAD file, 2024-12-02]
Hardware/CAD_Files/Spice Base half.STL
397.9 x 7.62 x 267.5

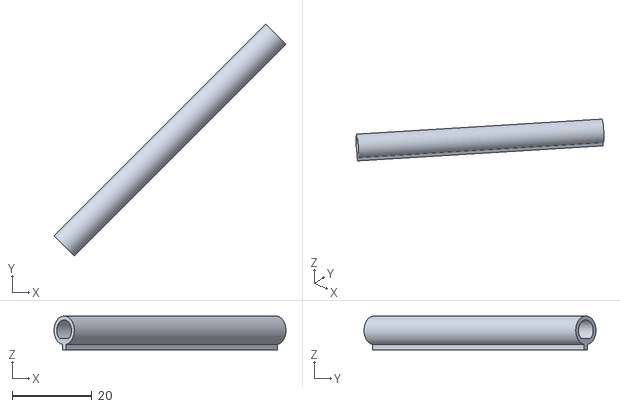
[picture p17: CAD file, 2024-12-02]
Hardware/CAD_Files/Auger Shaft.stl
58.1 x 58.1 x 8.52

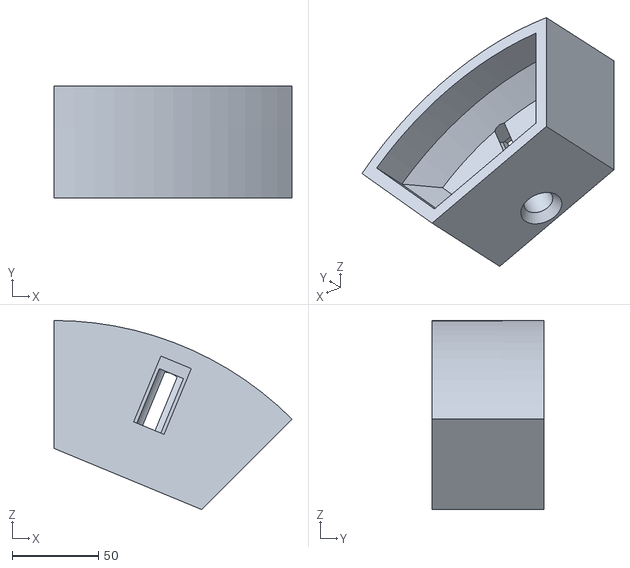
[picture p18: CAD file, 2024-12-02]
Hardware/CAD_Files/Spice Holder.STL
137.8 x 64.8 x 109.5

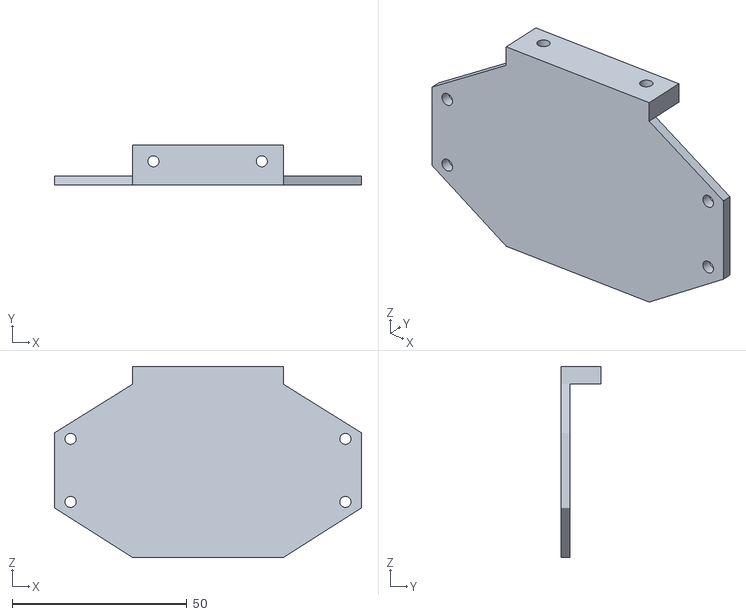
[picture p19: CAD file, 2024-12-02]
Hardware/CAD_Files/Motor1 Base1.STL
87.9 x 11.4 x 54.7

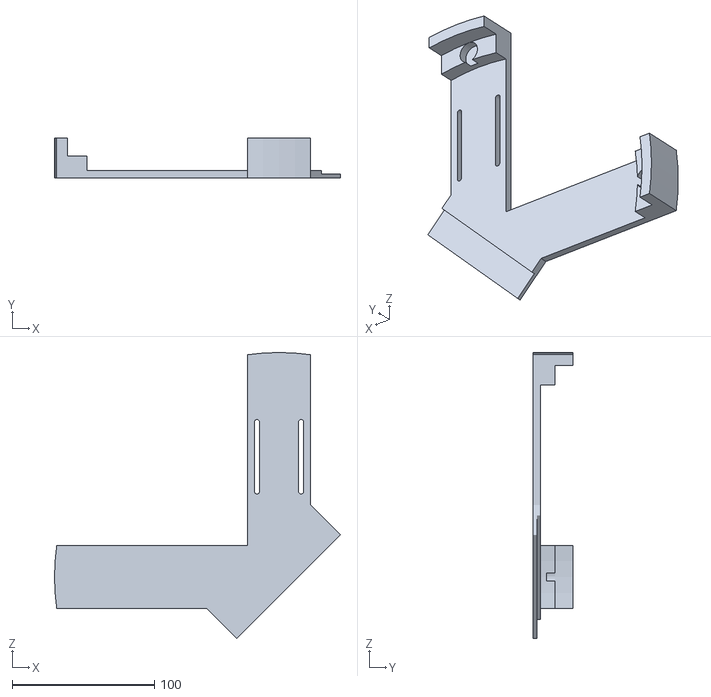
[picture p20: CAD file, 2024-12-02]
Hardware/CAD_Files/Turntable Base Half2.STL
200.7 x 27.8 x 200.7

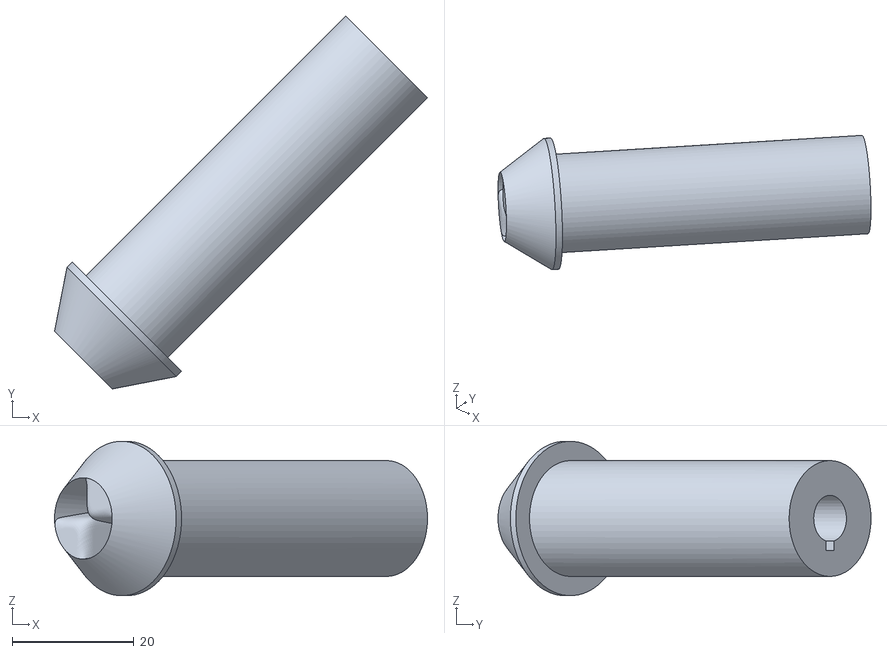
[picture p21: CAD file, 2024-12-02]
Hardware/CAD_Files/Shaft Extension.STL
61.4 x 61.4 x 25.4

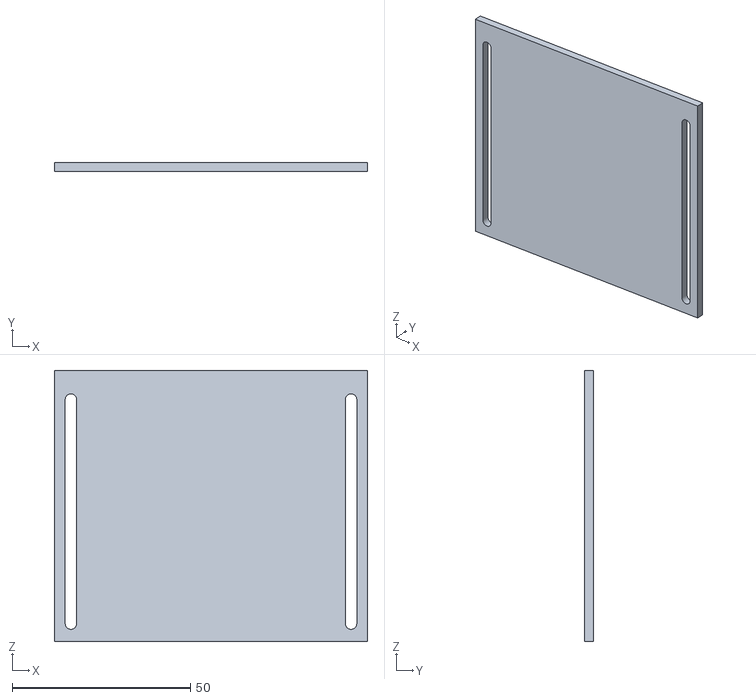
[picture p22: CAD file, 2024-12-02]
Hardware/CAD_Files/Motor1 Base2.STL
87.9 x 2.54 x 76.2

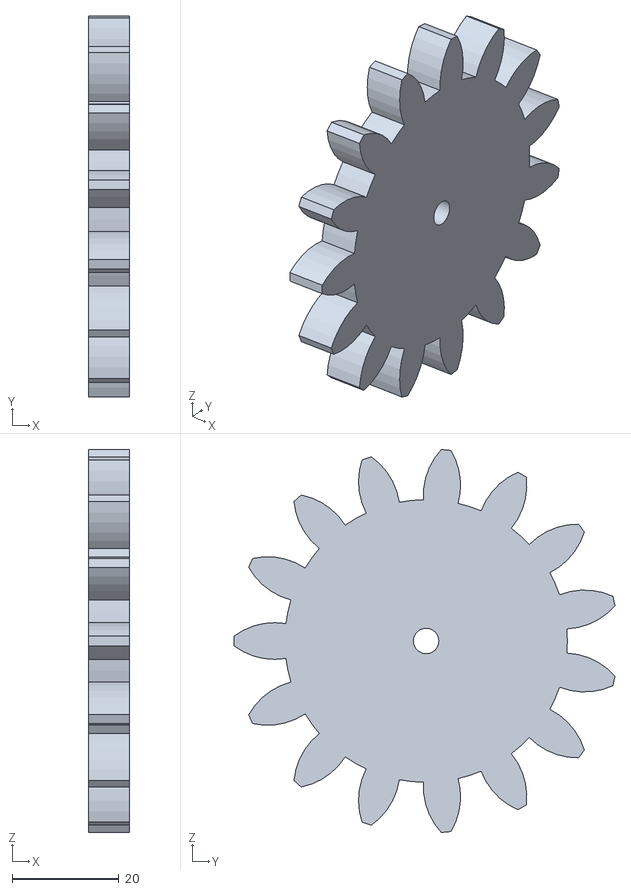
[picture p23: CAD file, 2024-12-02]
Hardware/CAD_Files/spur gear_ai.STL
7.62 x 71.3 x 71.7

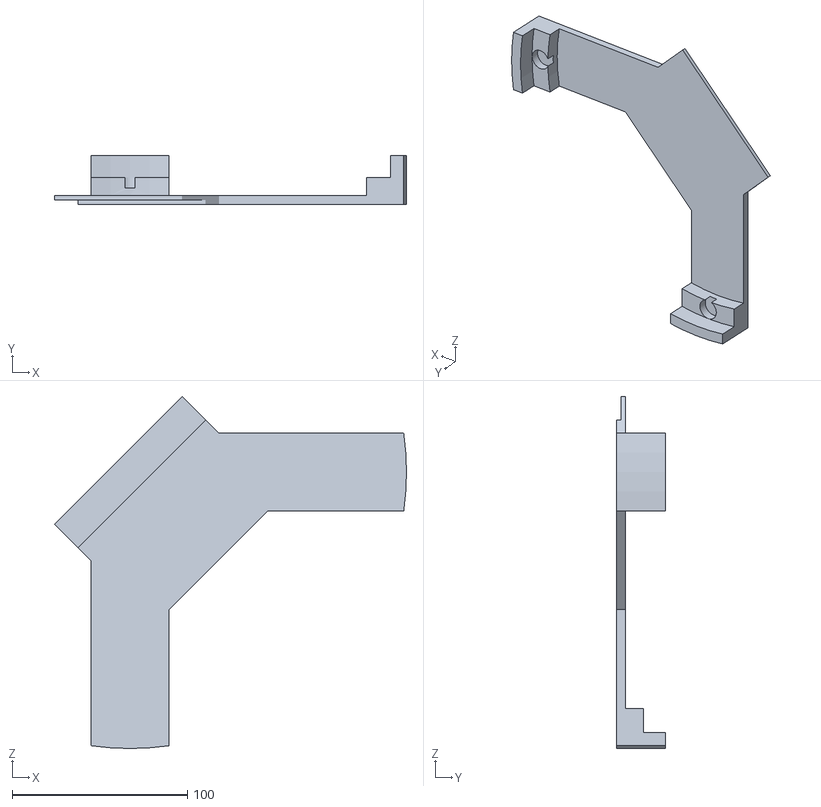
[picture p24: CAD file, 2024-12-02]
Hardware/CAD_Files/Turntable Base Half1.STL
200.7 x 27.8 x 200.7

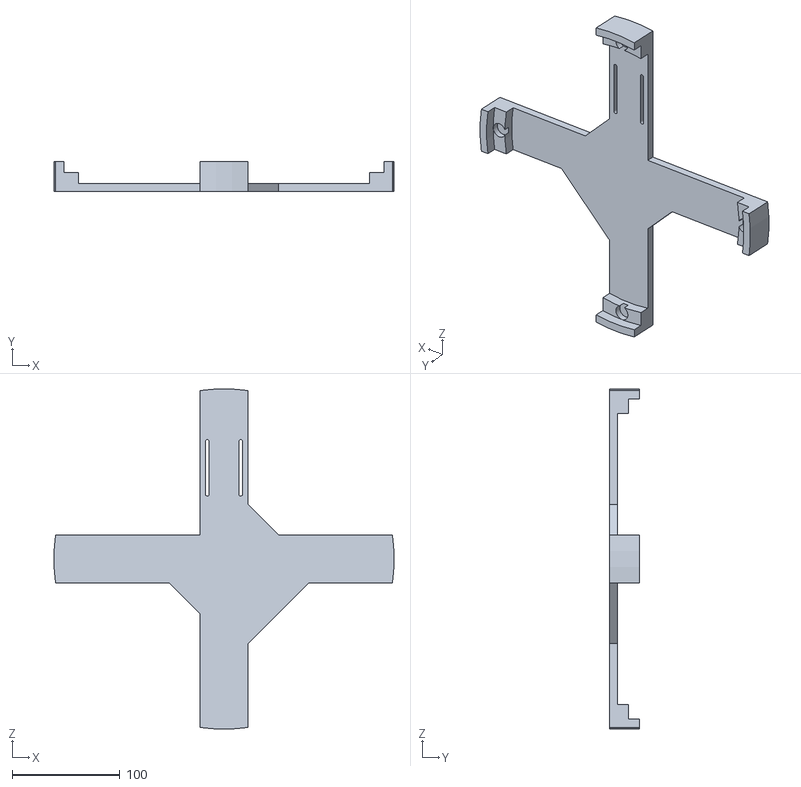
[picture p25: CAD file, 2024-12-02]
Hardware/CAD_Files/Turntable Base.STL
314.9 x 27.8 x 314.9

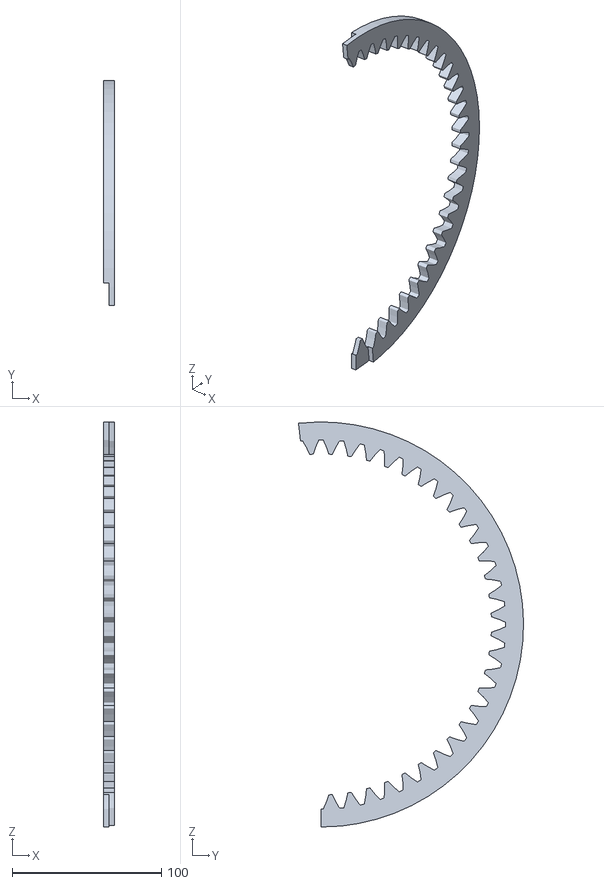
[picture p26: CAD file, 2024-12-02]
Hardware/CAD_Files/Internal gear half.STL
7.62 x 150.9 x 271.5

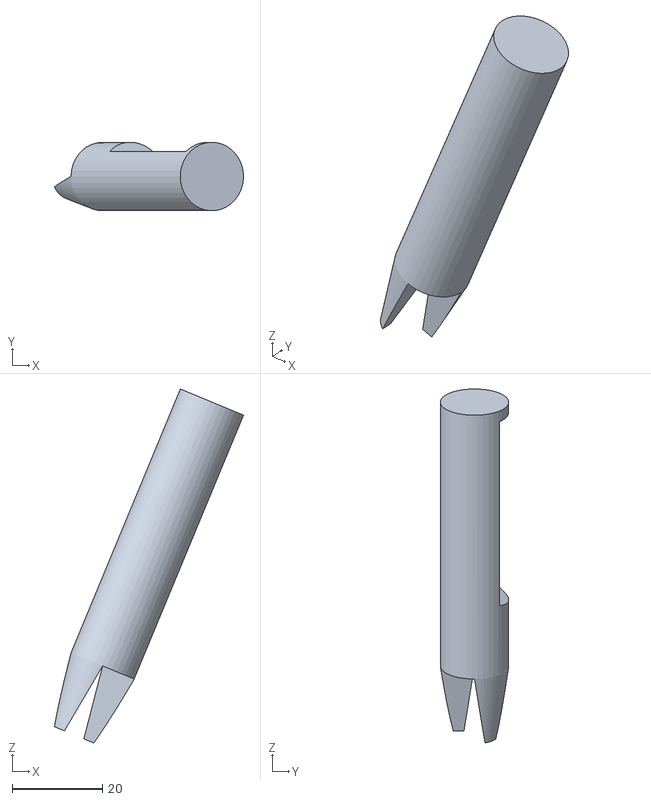
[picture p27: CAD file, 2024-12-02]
Hardware/CAD_Files/Auger.STL
41.9 x 15.2 x 78.4

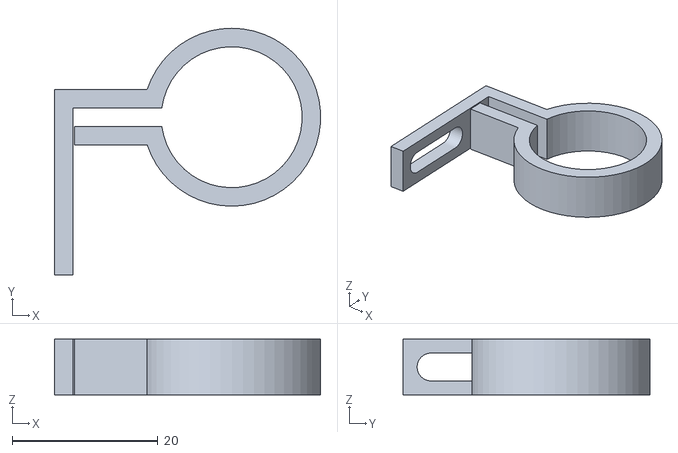
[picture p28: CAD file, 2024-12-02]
Hardware/CAD_Files/Clutch.STL
36.4 x 33.8 x 7.62

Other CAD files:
Hardware/CAD_Files/Spice Base.STL

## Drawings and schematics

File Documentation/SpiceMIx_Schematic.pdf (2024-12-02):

## PB0 PB1 PB2 PB3 PB4 PB5 PB6 PB7

INDEX | 17 DIR 9 | STEP 10 | PDN 11 | UART 12 | SPRD 13 | MS2 14 | MS1 15 | EN 16 | DIAG | 18 AUGDRIVER | GND | 1*2 VIO | 2 M1B | 5 M1A | 6 M2A | 4 M2B | 3 VM | 8

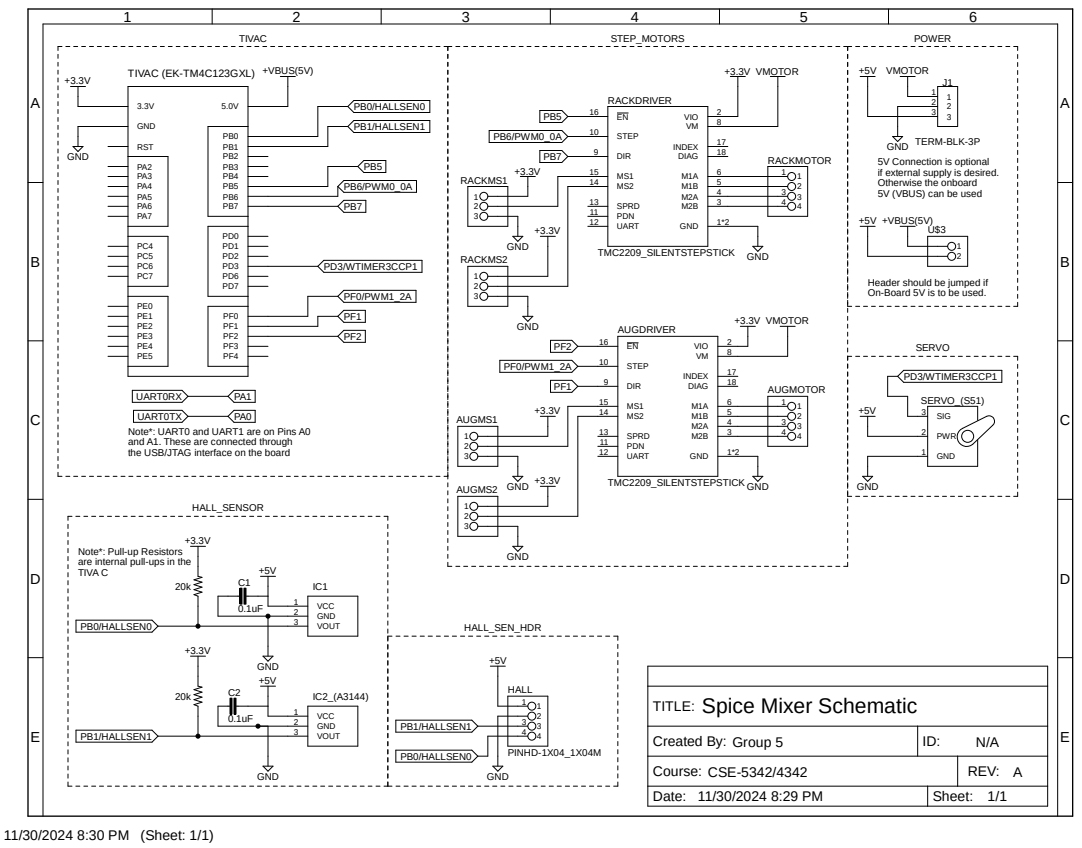
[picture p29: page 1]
11/30/2024 8:30 PM (Sheet: 1/1); STEP_MOTORS; POWER; SERVO; HALL_SEN_HDR; TIVAC; HALL_SENSOR; GND; +3.3V VMOTOR; +VBUS(5V); TMC2209_SILENTSTEPSTICK; +5V VMOTOR; PINHD-1X04_1X04M; 3.3V GND; 5.0V RST; RACKDRIVER GND; 1*2 VIO; INDEX; 17 DIR 9; STEP 10; PDN 11; UART 12; SPRD 13; DIAG; RACKMS1; 1 2 3 RACKMS2; 1 2 3 AUGMS1; 1 2 3 AUGMS2; RACKMOTOR; 2 SERVO_(S51) PWR 2; SIG 3; GND 1 HALL; IC1VCC 1; GND 2; VOUT 3; IC2_(A3144) VCC 1; PF0/PWM1_2A; PB6/PWM0_0A; PD3/WTIMER3CCP1; PB0/HALLSEN0; PB1/HALLSEN1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

TERM-BLK-3P GND
5V Connection is optional
if external supply is desired.
Otherwise the onboard
5V (VBUS) can be used
4 AUGMOTOR

Header should be jumped if
On-Board 5V is to be used.

UART0RX
UART0TX
Note*: UART0 and UART1 are on Pins A0
and A1. These are connected through
the USB/JTAG interface on the board

Note*: Pull-up Resistors
are internal pull-ups in the
TIVA C

Spice Mixer Schematic

Created By: Group 5 | ID: N/A

Course: CSE-5342/4342 | REV: A
Date: | Sheet: 11/30/2024 8:29 PM 1/1

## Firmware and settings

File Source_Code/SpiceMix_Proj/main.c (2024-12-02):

/* =======================================================
 * File Name: main.c
 * =======================================================
 * File Description: Main Program File
 * =======================================================
 */

#include <stdint.h>
#include <stdio.h>
#include <stdbool.h>
#include <string.h>
#include <stdlib.h>
#include "System.h"
#include "StepMotor.h"
#include "Servo.h"
#include "MotorControl.h"
#include "eepromControl.h"
#include "eeprom.h"
#include "uart0.h"
#include "parsing.h"
#include "UIControl.h"

#define NUMOFCMDS 11

// If a command is added here, don't forget to add
// verbage to the displayHelpPage function for syntax usage.
UICmdStructType commands[NUMOFCMDS] = 
{
    {"spice",  3},
    {"recipe", 2},
    {"view",   2},
    {"check",  2},
    {"save",   2},
    {"delete", 2},
    {"refill", 3},
    {"change", 1},
    {"home",   1},
    {"reset",  1},
    {"stop",   1},
};

void displayHelpPage(void)
{
    putsUart0("=====================================================================\n");
    putsUart0("Here are all the available commands and their usage:\n");
    putsUart0("=====================================================================\n");
    putsUart0("\n");
    putsUart0("spice <name> <qty>   - Dispenses the qty of a defined spice.\n");
    putsUart0("                       Note: qty is in half-teaspoon measurements.\n");
    putsUart0("\n");
    putsUart0("recipe <name>        - Dispenses the specified recipe.\n");
    putsUart0("\n");
    putsUart0("view <item>          - View a list of stored items. view Spices will \n");
    putsUart0("                       display a list of the stored spices and their \n");
    putsUart0("                       remaining quantities. view Recipes will display \n");
    putsUart0("                       a list of stored recipes\n");
    putsUart0("\n");
    putsUart0("check <recipe>       - View the elements of a stored recipe. <recipe> \n");
    putsUart0("                       must be the name of a stored recipe.\n");
    putsUart0("\n");
    putsUart0("save <recipe>        - Save a new recipe or update an existing recipe \n");
    putsUart0("                       <recipe> can either be a new name or the name \n");
    putsUart0("                       of an existing recipe\n");
    putsUart0("\n");
    putsUart0("delete <recipe>      - Delete an existing recipe <recipe> must be the \n");
    putsUart0("                       name of a stored recipe.\n");
    putsUart0("\n");
    putsUart0("refill <spice> <qty> - Refill a spice with a specified quantity \n");
    putsUart0("                       <spice> must be the name of an existing spice \n");
    putsUart0("\n");
    putsUart0("change               - Change or Update the name of an existing spice \n");
    putsUart0("\n");
    putsUart0("home                 - Perform the homing of the rack to reset the \n");
    putsUart0("                       the home position \n");
    putsUart0("\n");
    putsUart0("reset                - Reset the system. This will reset the system \n");
    putsUart0("                       back to the default values. This will also \n");
    putsUart0("                       remove all stored recipes. \n");
    putsUart0("\n");
    putsUart0("stop                 - Turns off all motors. Homing must be performed\n");
    putsUart0("                       after this command is used to ensure correct\n");
    putsUart0("                       home state\n");
    putsUart0("=====================================================================\n");
    putsUart0("\n");
}

int main(void)
{
    // Initialize System and Hardware Peripherals
    System_Init();
    StepMotorInit();
    ServoInit();
    HallSensorInit();

    // Initialize UARTspi
    initUart0();
    setUart0BaudRate(115200, 40e6);

    // Initialize EEPROM and UI List
	initEeprom();
    initSpiceData(false);
    initSpiceList();
    initRecipeList();

    USER_DATA data;
    int8_t code = -1;

    bool homing_performed = false;

    while(true)
    {
        putsUart0("\n============================= MAIN MENU =============================\n");
        putsUart0("Enter a command (Press Enter for a list of commands): ");
        clearBuffer(&data);
        getsUart0(&data);
        putsUart0("\n");
        code = identifyCommand(&data, commands, NUMOFCMDS);

        switch(code)
        {
            case 0:
                if(homing_performed == false)
                {
                    putsUart0("====================== WARNING ======================\n");
                    putsUart0("Homing has not been performed since the last start-up!\n");
                    putsUart0("or emergency stop. Please home the rack using the home\n");
                    putsUart0("command before dispensing\n");
                }
                else
                {
                    dispenseSpice(&data);
                }
                break;
            case 1:
                if(homing_performed == false)
                {
                    putsUart0("====================== WARNING ======================\n");
                    putsUart0("Homing has not been performed since the last start-up!\n");
                    putsUart0("or emergency stop. Please home the rack using the home\n");
                    putsUart0("command before dispensing\n");
                }
                else
                {
                    dispenseRecipe(&data);
                }
                break;
            case 2:
                viewItems(&data);
                break;
            case 3:
                printRecipe(&data);
                break;
            case 4:
                saveRecipe(&data);
                break;
            case 5:
                deleteRecipe(&data);
                break;
            case 6:
                refillSpice(&data);
                break;
            case 7:
                changeSpice(&data);
                break;
            case 8:
                UIRackHome();
                homing_performed = true;
                break;
            case 9:
                resetSystem(&data);
                break;
            case 10:
                putsUart0("Turning Off all Motors\n");
                TurnOffMotor(RACK);
                TurnOffMotor(AUGER);
                homing_performed = false;
                break;
            default:
                putsUart0("ERROR: Command not recognized.\n");
                displayHelpPage();
                break;
        }
    }
}

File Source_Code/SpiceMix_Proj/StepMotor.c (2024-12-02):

/* =======================================================
 * File Name: StepMotor.c
 * =======================================================
 * File Description: Stepper Motor Library
 * Contains variables and functions
 * used for stepper motor initialization and control
 * =======================================================
 */

#include "StepMotor.h"
#include "tm4c123gh6pm.h"
#include "wait.h"

/*========================================================
 * Variable Definitions
 *========================================================
 */

// For Debugging Remove the Static
MotorDataStructType MotorData[2] =
{
    {OFF, CW, NOTHOME, 0, 0, 3},
    {OFF, CW, NOTHOME, 0, 0, 3}
};

/*========================================================
 * Function Declarations
 *========================================================
 */

 /* =======================================================
  * Function Name: StepMotorInit
  * =======================================================
  * Parameters: None
  * Return: None
  * Description: Initializes the peripherals needed for
  * Stepper Motor Control. The system utilizes two stepper
  * motors. This will initialize Port B5-7 and PortF0-3
  * for the motor output. Additionally PWM module 0 (PB4-7)
  * are initialized for PWM control
  * =======================================================
  */
void StepMotorInit(void)
{
    // Enable GPIO PORTB, and PORTF
    SYSCTL_RCGCGPIO_R |= SYSCTL_RCGCGPIO_R1 | SYSCTL_RCGCGPIO_R5;
    SYSCTL_RCGCPWM_R |= SYSCTL_RCGCPWM_R0 | SYSCTL_RCGCPWM_R1;  // PWM0 Module for Motor Control
    _delay_cycles(3);

    // Initialize PORTB (Motor Output and PWM Control)
    GPIO_PORTB_DIR_R |= 0xE0;           // Enable PB5-7 as outputs
    GPIO_PORTB_DEN_R |= 0xE0;           // Set Digital Enable
    GPIO_PORTB_AFSEL_R |= 0x40;         // Enable Alternate Function (for PWM) PORTB6
    GPIO_PORTB_PCTL_R &= ~0x0F000000;   // Clear bits for enabling
    GPIO_PORTB_PCTL_R |= 0x04000000;    // Enable M0PWM0 (PB6))

    // Initialize PORTF (Motor Output 2)
    GPIO_PORTF_LOCK_R = 0x4C4F434B;     // Unlock PORTF0
    GPIO_PORTF_CR_R |= 0x01;            // Unlock PORTF0
    GPIO_PORTF_DIR_R |= 0x07;           // Enable PORTF0,1,2, as outputs
    GPIO_PORTF_DEN_R |= 0x07;           // Enable PORTF0,1,2 as digital pins
    GPIO_PORTF_AFSEL_R |= 0x01;         // Enable Alternate Function (for PWM) PORTF0-2
    GPIO_PORTF_PCTL_R &= ~0x0005;       // Clear bits for enabling
    GPIO_PORTF_PCTL_R |= 0x0005;        // Enable M1PWM2 (PF0)

    // Initialize PWM Module 0
    SYSCTL_SRPWM_R = SYSCTL_SRPWM_R0| SYSCTL_SRPWM_R1;   // Reset PWM1 module
    SYSCTL_SRPWM_R = 0;     // Turn off Reset
    PWM0_0_CTL_R = 0;       // Turn-off PWM1 Gen1 (Drives PWM2/3)
    PWM1_2_CTL_R = 0;       // Turn-off PWM1 Gen1 (Drives PWM2/3)

    // Enable Global Sync for PWM Generators
    PWM0_0_CTL_R |= 0x3F8;
    PWM1_2_CTL_R |= 0x3F8;

    // Set for PWM high when counter = comparator. Low when counter = 0
    // Generator B configured to look at comparator A
    PWM0_0_GENA_R = PWM_0_GENA_ACTCMPAD_ONE | PWM_0_GENA_ACTZERO_ZERO;
    PWM1_2_GENA_R = PWM_1_GENA_ACTCMPAD_ONE | PWM_1_GENA_ACTZERO_ZERO;

    // Set PWM Frequency
    PWM0_0_LOAD_R = 0xFFFF; //Max load = lowest RPM
    PWM1_2_LOAD_R = 0xFFFF; //Max load = lowest RPM

    // PWM Off on Power-up (Duty cycle = 0)
    PWM0_0_CMPA_R = 0x0FF;
    PWM1_2_CMPA_R = 0x0FF;

    PWM0_INTEN_R |= 0x01;
    PWM1_INTEN_R |= 0x04;

    NVIC_EN0_R |= 1 << (INT_PWM0_0 - 16);   // Register the PWM0 Interrupt
    NVIC_EN4_R |= 1 << (INT_PWM1_2 - 16-128);   // Register the PWM0 Interrupt
    
    // Enable PWM Generators
    PWM0_0_CTL_R |= 0x01;
    PWM0_1_CTL_R |= 0x01;
    PWM0_ENABLE_R = 0x00;;

    PWM1_2_CTL_R |= 0x01;
    PWM1_ENABLE_R = 0x00;

    // Sync 
    PWM0_CTL_R = 0xF;
    PWM1_CTL_R = 0xF;

    // Turn Off Motors on Start-up
    MOTOR0EN = 1;
    MOTOR1EN = 1;
}

/* =======================================================
 * Function Name: HallSensorInit
 * =======================================================
 * Parameters: None
 * Return: None
 * Description: This function initializes the peripherals
 * needed for the hall sensor detection. This will
 * initialize PORTB0 and 1 for the hall sensor.
 * =======================================================
 */
void HallSensorInit(void)
{
    // Enable GPIO PORTB
    SYSCTL_RCGCGPIO_R |= SYSCTL_RCGCGPIO_R1;
    _delay_cycles(3);

    // Initialize PORTB (Hall Sensor Input)
    GPIO_PORTB_DIR_R &= ~HALSEN_MASK;   // Enable PB0/1 as Inputs
    GPIO_PORTB_DEN_R |= HALSEN_MASK;    // Set Digital Enable
    GPIO_PORTB_PUR_R |= HALSEN_MASK;    // Set Internal Pull-Up

    // Configuring GPIO Interrupts
    GPIO_PORTB_IM_R &= ~HALSEN_MASK;    // Mask out interrupts to prevent false trip during config
    GPIO_PORTB_IS_R &= ~HALSEN_MASK;    // Set for interrupt on edge detect
    GPIO_PORTB_IBE_R |= HALSEN_MASK;   // Interrupt on both edges
    GPIO_PORTB_ICR_R |= HALSEN_MASK;    // Clear any pending Interrupts
    GPIO_PORTB_IM_R |= HALSEN_MASK;     // Turn on Interrupts
    NVIC_EN0_R |= 1 << (INT_GPIOB - 16);    // Enable interrupts for Port D
}

/* =======================================================
 * Function Name: CommandMotor
 * =======================================================
 * Parameters: MotorID, microsteps, speed
 * Return: None
 * Description: This function will begin the process of
 * commanding a stepper motor specified by the motorID.
 * The function will set the direction pins and enable 
 * the requested motor. The function will also enable the
 * corresponding PWM interrupt to begin the motor command.
 * =======================================================
 */
void CommandMotor(uint32_t motorID, int32_t microsteps, uint16_t speed)
{
    uint32_t dir = CW;
    int32_t sign = 1;

    SetMotorSpd(motorID, speed);

    if (microsteps < 0)
    {
        dir = CCW;
        sign = -1;
    }
    
    MotorData[motorID].steps = (uint32_t) microsteps*sign;

    switch (motorID)
    {
    case 0:
        MOTOR0DIR = dir;
        // Enable Load Interrupt for Gen 0

        PWM0_0_INTEN_R |= 0x02;
        break;
    case 1:
        MOTOR1DIR = dir;
        // Enable Load Interrupt for Gen 0
        PWM1_2_INTEN_R |= 0x02;
        break;
    default:
        break;
    }
}
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

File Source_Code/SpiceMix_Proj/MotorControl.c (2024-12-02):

/* =======================================================
 * File Name: MotorControl.c
 * =======================================================
 * File Description: Contains variables and functions
 * used for controlling stepper and servo motors.
 * =======================================================
 */

#include "MotorControl.h"
#include "tm4c123gh6pm.h"
#include "wait.h"
#include "StepMotor.h"
#include "Servo.h"

/*========================================================
 * Variable Definitions
 *========================================================
 */
uint16_t rack_pos;

// System Calibration Values
int16_t HOME_OFFSET = -500;
int16_t AUG_OFFSET = 320;
uint16_t SVO_ENG_POS = 90;
uint16_t SVO_DIS_POS = 160;


/*========================================================
 * Function Declarations
 *========================================================
 */

/* =======================================================
 * Function Name: StepRackHome
 * =======================================================
 * Parameters: None
 * Return: None
 * Description: This function performs the homing of the
 * main rack. The rack motor is commanded to turn until
 * the hall sensors located at the home position, indicate
 * the rack is "home". The home_status state is set from
 * the hall sensor interrupt. As the rack approaches home,
 * the rack will be slowed until both sensors indicate
 * home. In the event home is never indicated, an
 * "HOME FAIL" error code will be returned
 * =======================================================
 */
uint16_t StepRackHome(void)
{
    MotorHomeStatEnumType home_status = NOTHOME;
    MotorRunStatEnumType run_status = RUNNING;
    bool nearhome_pv = false;

    home_status = GetMotorHomeStatus(RACK);

    if (home_status != HOME)
    {
        // Command the Rack Motor to make 3 full rotations
        CommandMotor(RACK, (USTEPFULL360 * 3 * GEARRATIO), 10);

        run_status = GetMotorRunStatus(RACK);
        waitMicrosecond(1000);  // Wait atleast 1ms to allow motor to start running

        while (home_status != HOME && run_status != HALTED)
        {
            home_status = GetMotorHomeStatus(RACK);
            run_status = GetMotorRunStatus(RACK);
            
            // If Approaching Home position slow down.
            if (home_status == NEARHOME)
            {
                // If first transition to near home slow down the motor
                if (nearhome_pv == false)
                {
                    SetMotorSpd(RACK, 6);
                    nearhome_pv = true;
                }
            }
            else
            {
                // If first transition out of near home, increase speed
                if (nearhome_pv == true)
                {
                    SetMotorSpd(RACK, 10);
                    nearhome_pv = 0;
                }
            }
        }

        if (home_status == HOME)
        {

            waitMicrosecond(100000);  // Wait atleast 1ms to allow motor to start running
            CommandMotor(RACK, HOME_OFFSET, 6);
            //TurnOffMotor(RACK);
            // Reset Rack position to 0 (Home);
            rack_pos = 0;
        }
        else
        {
            // Failed to find home before Motor Timeout
            if (run_status == HALTED)
            {
                run_status = FAILED;
                return ERRORHOMEFAIL;
            }
        }
    }

    // Reset Rack Motor Speed to default
    SetMotorSpd(RACK, 20);

    return 0;
}

/* =======================================================
 * Function Name: SetRackPos
 * =======================================================
 * Parameters: pos
 * Return: None
 * Description: This function will command the rack motor
 * to turn the rack to a specified position. Based on
 * the given position (0-7) the angle and corresponding
 * commanded steps is calculated. The function will
 * wait for the motor to execute and will return once
 * all steps have been executed.
 * =======================================================
 */
void SetRackPos(uint16_t pos)
{
    MotorRunStatEnumType status = OFF;
    uint16_t angle = 0;

    // Limit Position input
    if (pos > 7)
    {
        pos = 7;
    }

    // Calculate the required angle
    angle = pos*45;

    // Calculate position difference
    float delta = angle - rack_pos;

    // Store new position
    rack_pos = angle;

    // Calculate shortest distance
    if(delta > 180)
    {
        // Subtract 360 to obtain CCW command
        delta = delta - 360;
    }
    else
    {
        if (delta < -180)
        {
            // Add 360 to obtain CW command
            delta = delta + 360;
        }
    }

    // Convert angle to microsteps
    // NOTE: This will be multiplied by some gain
    // factor for the gear ratio
    int32_t microsteps = (int32_t) (delta/MICROSTEPSF)* GEARRATIO;

    // Command the new position
    CommandMotor(RACK, microsteps, 30);

    while (status != HALTED)
    {
        status = GetMotorRunStatus(RACK);
    }

    //Wait half a second to let motor come to a full stop
    waitMicrosecond(500000);
}

/* =======================================================
 * Function Name: SetAugerPos
 * =======================================================
 * Parameters: rotations
 * Return: None
 * Description: This function commands the auger motor
 * to rotate a specified amount of full rotations.
 * The function will wait for the motor to complete
 * its command and will return once all steps have been
 * executed.
 * =======================================================
 */
void SetAugerPos(uint16_t rotations)
{
    MotorRunStatEnumType status = OFF;

    // Calculate position difference
    float delta = 360*rotations;

    // Convert angle to microsteps
    int32_t microsteps = (int32_t) delta/MICROSTEPSF;

    // Rotate some additional steps to offset the auger screw for
    // the next load.
    microsteps = microsteps + AUG_OFFSET;
    CommandMotor(AUGER, microsteps, 35);

    while (status != HALTED)
    {
        status = GetMotorRunStatus(AUGER);
    }

    // De-energize the Auger Motor after moving since it
    // does not need to be held in place
    TurnOffMotor(AUGER);

    //Wait 10ms for motor to come to a stop
    waitMicrosecond(10000);
}

/* =======================================================
 * Function Name: TestMotors
 * =======================================================
 * Parameters: None
 * Return: None
 * Description: This function is debugging only and allows
 * for testing of the motrs and the hardware.
 * A breakpoint can be used to set the desired position
 * and rotation arguments.
 * =======================================================
 */
void TestMotors(void)
{



}
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

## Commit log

2024-10-10 Added PWM Control
2024-10-11 Fixed bug in PWM Init
2024-10-19 Added Servo Library and cleaned up Stepper Library
2024-10-19 Added Homing Function
    Cursed R9 and R10 need to be removed on the board so PD0 and PD1 are not tied to PB6/7
2024-10-21 Enhanced version of step control
    Stepping controlled by interrupts. Added additional organization which restricts access to certain motor member data
2024-10-21 Uploading RevA of Circuit Schematic
2024-10-21 Slight Revision to Schematic
    Added missing pull up and capacitor values
2024-10-30 Some bug fixes for MotorControl
    Fixed a couple of bugs that came with the transition to interrupts
    [MotorControl.c, StepMotor.c, main.c]
2024-10-30 Added wait times so the motors don't overrun each other
2024-11-07 MotorControlCode with Proper Drivers
2024-11-11 Added gear ratio
2024-11-11 Pushing initial EEPROM driver
    [EEPROM_MemoryMap.xlsx]
2024-11-11 Code Documentation
    [EEPROM_MemoryMap.xlsx]
2024-11-12 MotorControl Code Documentation
2024-11-16 Pushing motor calibration figures
2024-11-18 Modded Servo Output Pin and decreasing homing speed
    PD3 was used on the PCB instead of PD2 so minor adjustment to initialization to use WTIMER1B instead
2024-11-25 Finished prototype UI functions
2024-11-27 Implementing UI functions and Documenting UI.
    Moved UI Functions to separate UIControl.c/.h files to clean-up main and ease documentation.
    WriteRecipe was changed to saveRecipe to avoid confusion with the eeprom function. This function was also fully implemented to take user inptus
    nameSearch was modified to properly search to properly access and search the name.
    dispenseSpice: Added validation checks for the requested and remaining quantity.
    dispenseRecipe: Added validation checks for each spice against the requested vs remaining quantity.
    RecipeList was modified to be a 2D array with pre-allocated memory for up to MAXNAMESIZE characters. This was also corrected to use the MAXNUMRECP (m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
    [MotorControl.c, UIControl.c, eepromControl.c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]
2024-11-27 Implemented workaround to sprintf bug
    [main.c]
2024-11-28 Added refillSpice and ChangeSpice command
    WIP:
    This commit pushes additional commands as well as updates some commands to provide clarity
    The commands array and minfields array has been replaced with the commands structure (UICmdStructType) This allows for the min fields to be coupled to the command to ease maintainability.
    The identifyCommand was updated to support this change.
    refillSpice: Function adds capability to refill a specified spice with a given quantity.
    changeSpice: Function adds capability to change the name of a spice as well as update the quantity.
    UIRackHome: Function simply calls the StepRackHome function and checks for any errors to indicate to user.
    StepRackHome: Bu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
    [MotorControl.c, UIControl.c, main.c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]
2024-11-30 Final updates
    [EEPROM_MemoryMap.xlsx]
2024-12-01 Fixing some spelling mistakes and correcting code mistakes
    Realized full capacity is 96 (half teaspoons). 48 is the max capacity in teaspoons
    [MotorControl.c, Servo.c, UIControl.c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]
2024-12-01 Additional Bug Fix
    Added validation of recipe name in save command
    [UIControl.c, main.c]
2024-12-02 Adding CAM Files and CAD Files
    [Auger Shaft.stl, Auger.STL, Clutch.STL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]
